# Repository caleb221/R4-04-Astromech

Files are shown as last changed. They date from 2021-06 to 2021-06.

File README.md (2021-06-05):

# R4-04-Astromech
A small Astromech droid I decided to make
  
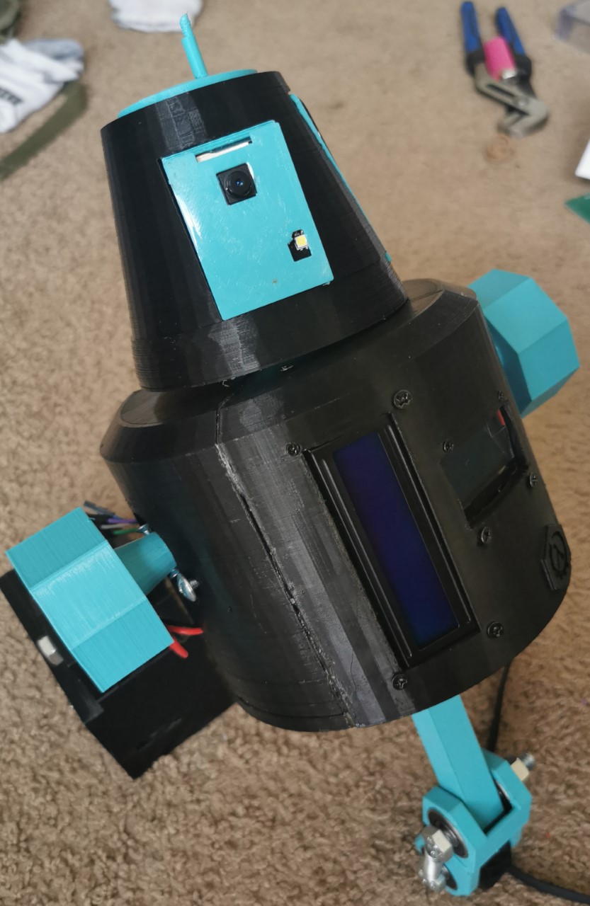
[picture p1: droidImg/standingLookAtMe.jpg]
the droid


# IN PROGRESS! CHECK BACK FOR UPDATES!
   --> finishing up the .ino control code, but hardware and ESP32 code is finished!
   
# Description  
 <h2>This is R4-04!</h2> <br>Designed with the <a href="https://starwars.fandom.com/wiki/R4_astromech_droid">R4 Astromech droid</a> in mind, but getting lost along the way resulted in R4-04, the droid for a galaxy not so far away.<br>
 This droid hosts its own WiFi network, and anyone in reach can accesss a web server holding a livestream of the IP camera and controls for the droid.<br>
 The IP of the droid's control server is printed on the bright blue LCD screen.<br>
 The droid is controlled using websocket communication on the ESP32 and relays information from the user to an Arduino Mega  controlling the motors via I2C commands. The Arduino also handles a self balancing routine, adjusting its shoulders with PID so that rougher terrain won't be a problem.<br> 
Along with the motor control, R4-04 also shows information concerning its environment on a second screen. The information is obtained via a BME280 Sensor.          

# Web App
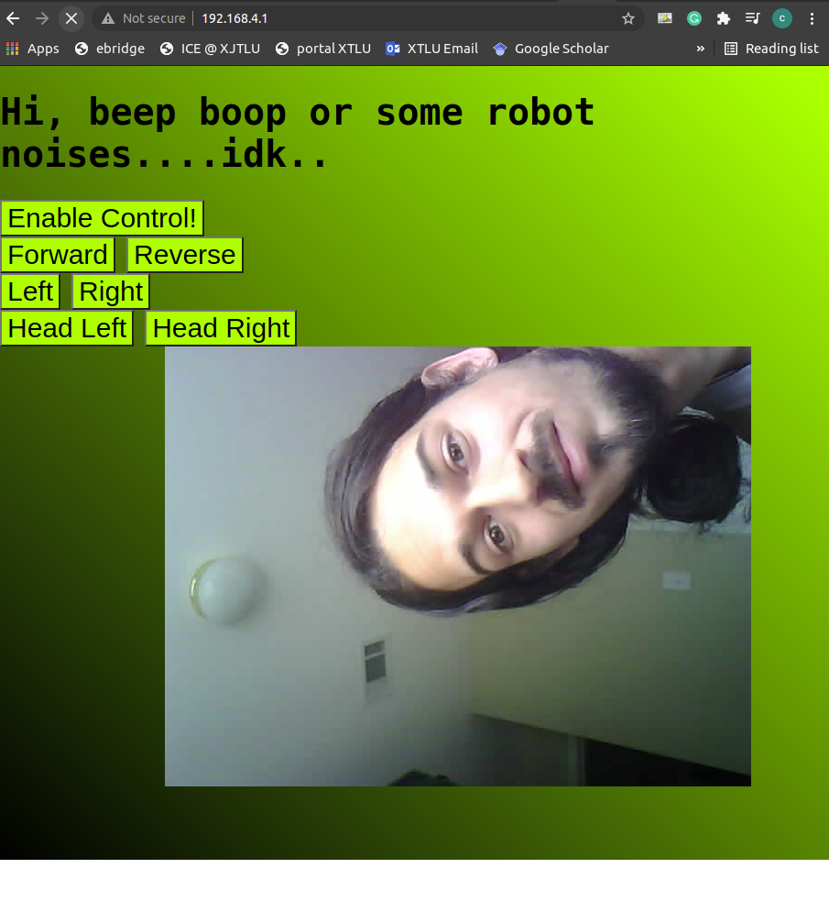
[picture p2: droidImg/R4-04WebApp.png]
the webApp

The droid implements a simple web application to control it along with a live video feed.
The feed is implemented using a timed function to poll the server to update it. It is sent in Jpeg format from the ESP32's onboard  OV2640 camera.<br>
The control buttons are implemented using websocket communication.<br>
Each button is given a specific ID command, which is passed through to the ESP32's I2C wires and sent to the arduino.<br>
Upon a new command event on the I2C wires the Arduino will perform the desired motor operations.

--> a CSS Transform on the img and possible pretty-ing up of the UI should be done in V2

# Stack
ESP32 Components:

    ESP-CAM
    ESP-WiFi
    SPIFFS
    freeRTOS
    I2C Driver
    HTTP-Server
 IDF-Version:
 
    ESP-IDF v4.4-dev-744-g1cb31e509

Arduino:
  
    Unistep2
    AdaFruit BME280
    GY521
    Wire
    U8G2Lib

# Hardware / Materials
    AI-Thinker ESP32-CAM 
    Arduino Pro Mega 2650 
    I2C 1602 LCD (blue) 
    I2C 1.3'' LCD Screen (white) 
    GYU-521 Accelerometer and Gyroscope 
    BME280 
    28byj-48 Stepper motor and 2003 ULN Driver (X3)
    L298N DC Motor Driver 
    DC "TT" Motor and wheel (X2)
    5V 30mA Mini Solar Panel 50x33mm (x2)
    4.8V NiMh 2200 mAh Battery (x2)
    608 Abec 9 Bearings (x8)<br>
    M4 X 30mm Screw and nuts X 6
    M3 x 35mm Screws X 4<br>
    M3 X various smaller sizes X 16
    5/16'' Bolt and nut (2.5+inches) X3 
    Springs that fit over the 5/16'' bolt (these are optional but help)
    Dupont Wires (Mostly Female to Female, but a Few male to Female)
    Various proto boards cut to size
    some passive components listed in the schematic
    Epoxy glue
    Hot glue 
    Solder
    PETG (testing parts took a lot of filament, not sure what the end result requires, also PLA should be fine)<br>

  # Tools
    3D printer (designed with the ender 3 in mind)
    Soldering Iron
    Screwdriver
    Hot Glue Gun
    Files / post processing tools
    Wire cutter
    A ventilated area
    Socket Wrench / Sockets come in handy 
    Something to spread epoxy with 
    Hacksaw
  
  # Schematic
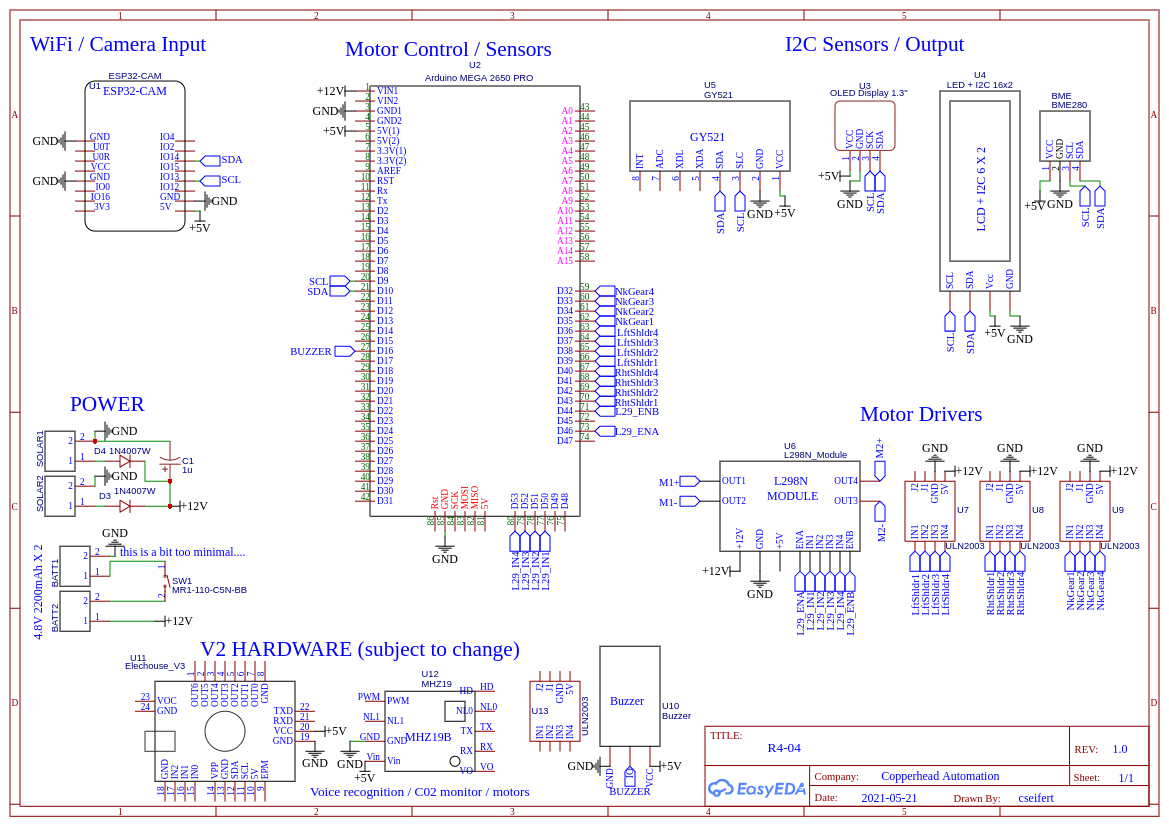
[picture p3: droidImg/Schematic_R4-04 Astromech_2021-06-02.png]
A simple schematic


# 3D Printer Settings

    Printer: Creality Ender 3 pro V2
    Filament: Duramic PETG
    Infill: 20% 
    Support: 2% everywhere
    Temp: 235
    Slicer: Cura
--> Slow on the first layer<br>
--> PLA Should be just fine for the parts as well, i just had PETG because it was cheaper at the time.<br>

# STL / FREECAD FILES
I designed the droid using FreeCAD, which is free and works on all major OS platforms.<br>
You are free to edit / change all designs, but please give a reference to the original!<br>
Printing all parts goes like this:<br>

    2 droidSolarPanelHolder1.stl, 1 of all others in the UPPER folder (head / neck)
    2 legs, 2 Shoulders, 2 FourthLeg_body.stl (Stepper holders), and 1 of each on the rest in the MIDDLE folder. (main body)
    2 droidFoot1.stl, 1 of each 3rd foot component in the LOWER folder. (lower assembly)

# Wiring / Testing

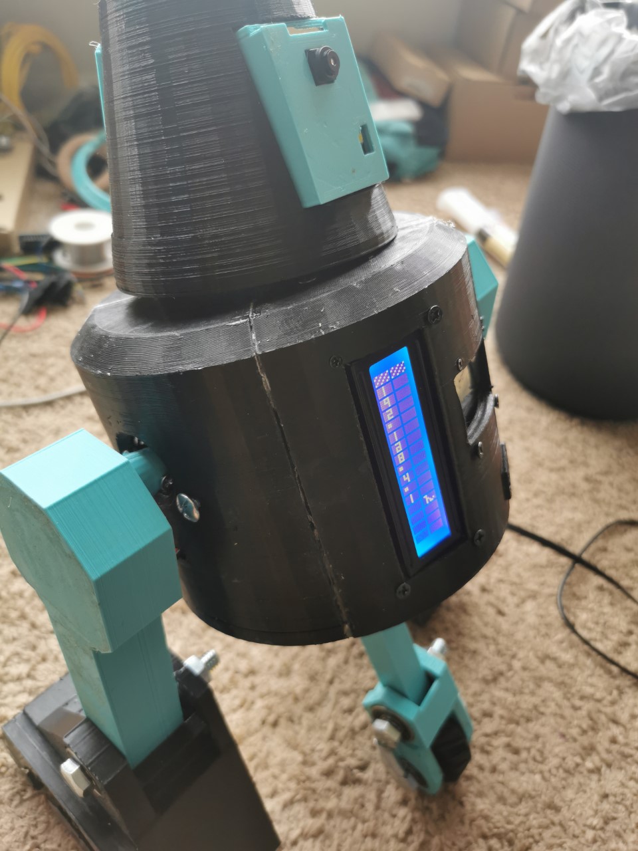
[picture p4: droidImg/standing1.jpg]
the droid
 

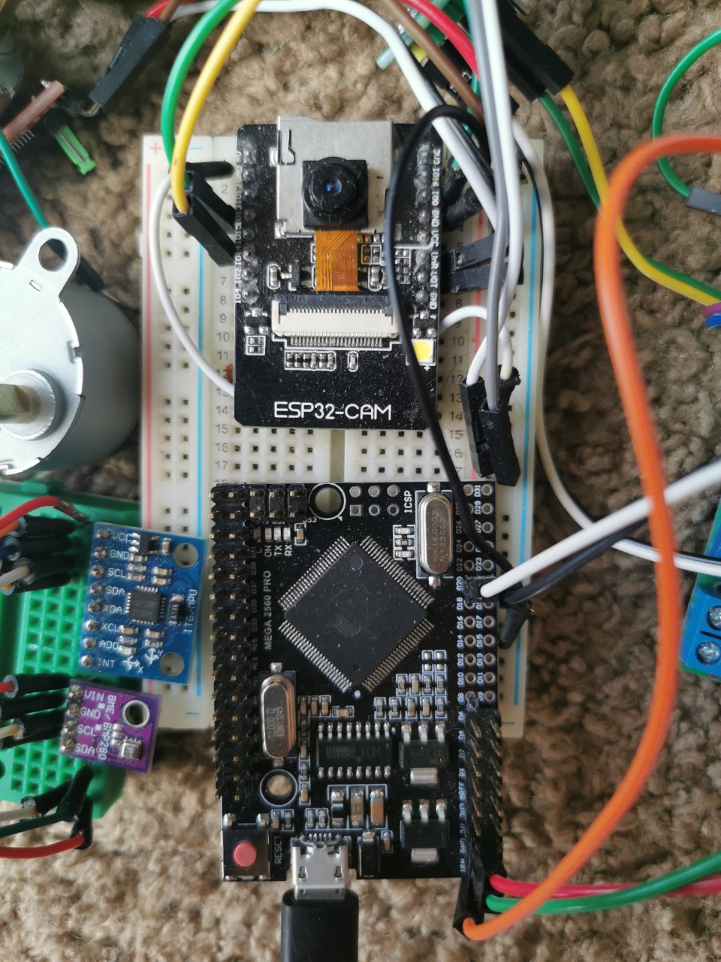
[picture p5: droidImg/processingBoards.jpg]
droid brain and heart
   
   
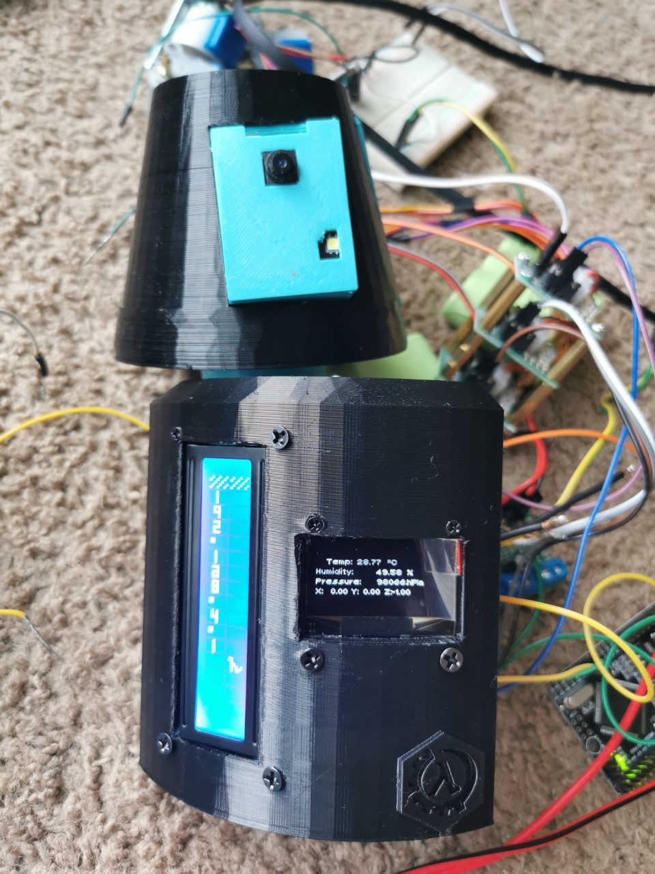
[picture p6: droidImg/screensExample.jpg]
Screen Test


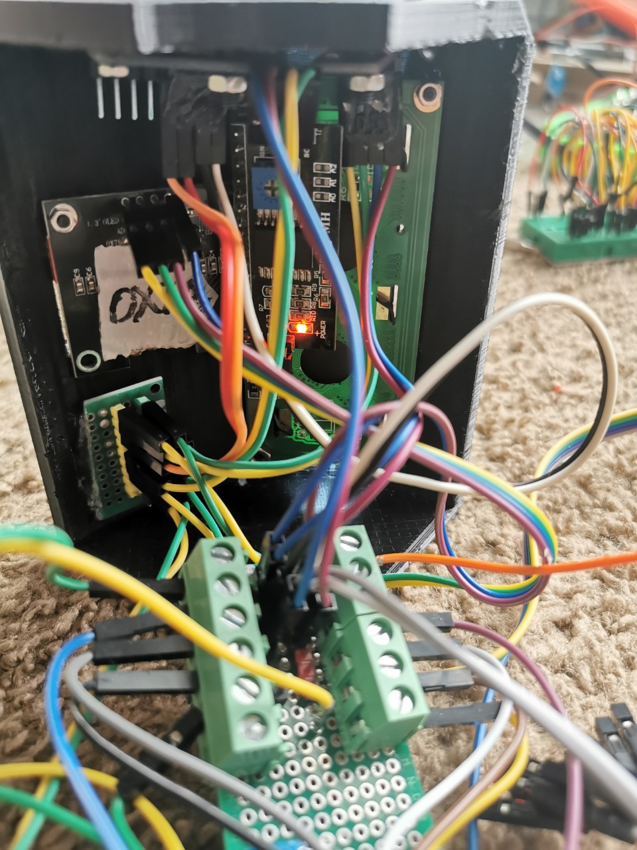
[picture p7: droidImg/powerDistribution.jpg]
   

# Mechanical Notes
The TT motor and wheel attatch to the foot using  M3 X 35MM screw and nuts. The leg is attached using 2 bearings and a 5/16'' bolt and nut.
There is a hole for the wires in the middle of the foot, as well as a space for them to fit on the side of the leg.<br>
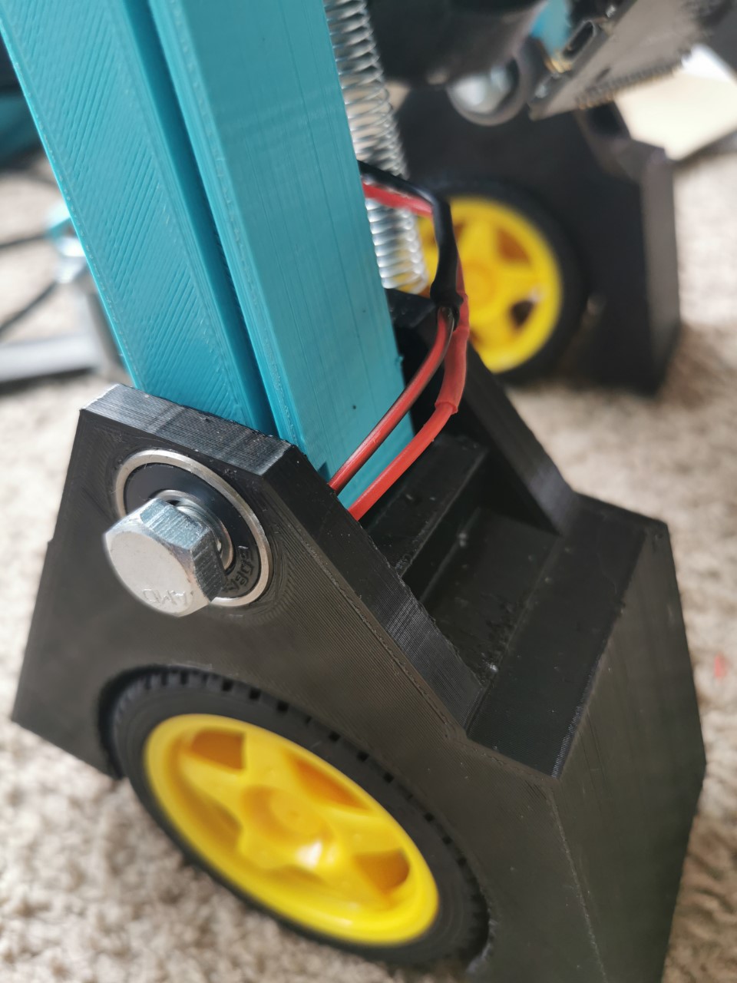
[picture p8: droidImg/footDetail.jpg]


<br>
The backside view of the droid.
There is a door that utilizes an M3 X 20 screw to hold both pieces in place.
Springs are attached from the stepper motor's M4 screw to the Foot's 5/16'' bolt. These are optional but help the droid remain standing under its own weight. The M4 screws I used hindered the neck from reaching the gear, this will be fixed in V2.
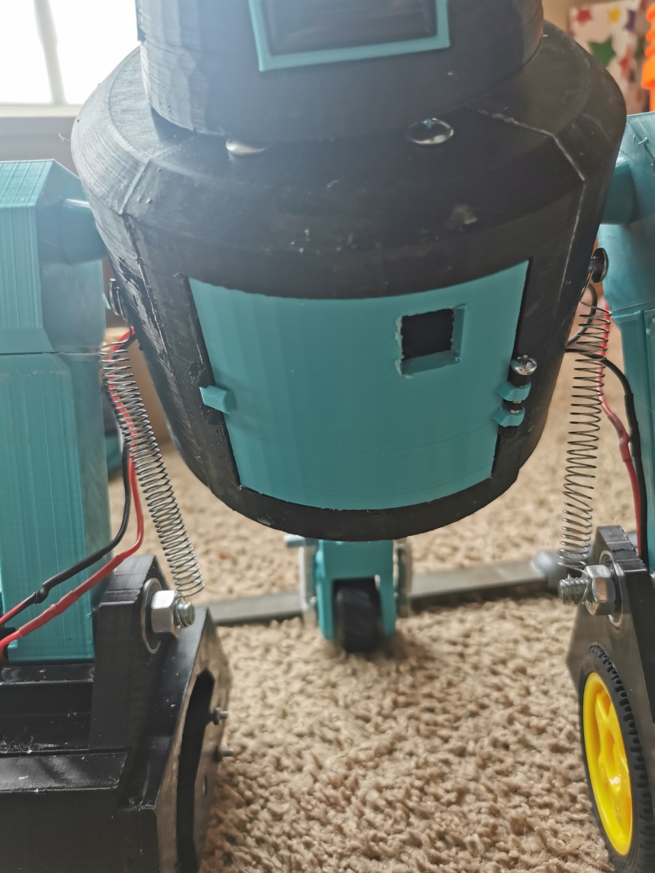
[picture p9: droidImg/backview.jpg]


<br>
There is a stepper motor with the smaller neck control gear attached to the top of the body using M4 screw and nuts. <br>
The neck assembly is glued into place on the head and is not glued to the body. SDA,SCL, 5V, and GND are run through the neck to reach the ESP32-CAM.<br>
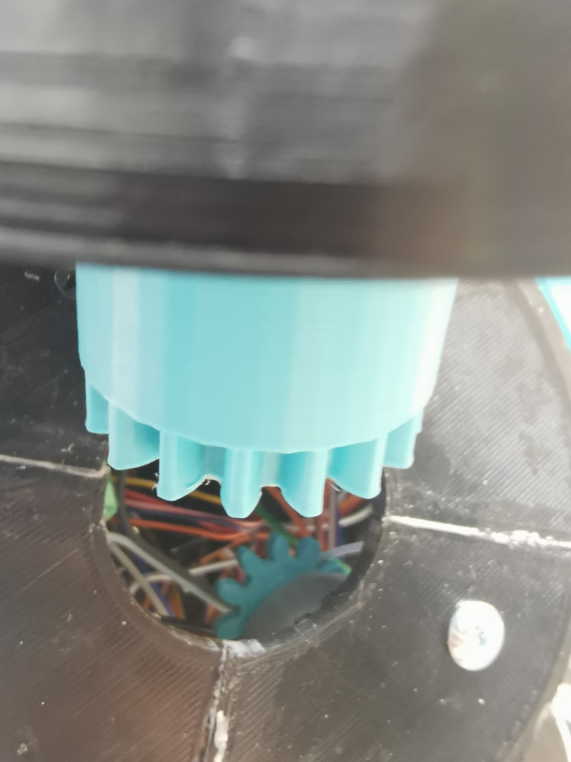
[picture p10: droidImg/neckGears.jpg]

<br>
The Front foot uses 4 bearings and an M3 x 8mm nut and screw that fits in the middle. Along with 2 5/16'' bolts to hold the wheel and leg in place. The springs are attached on the outside of each bolt which help restrict the freedom of movement.
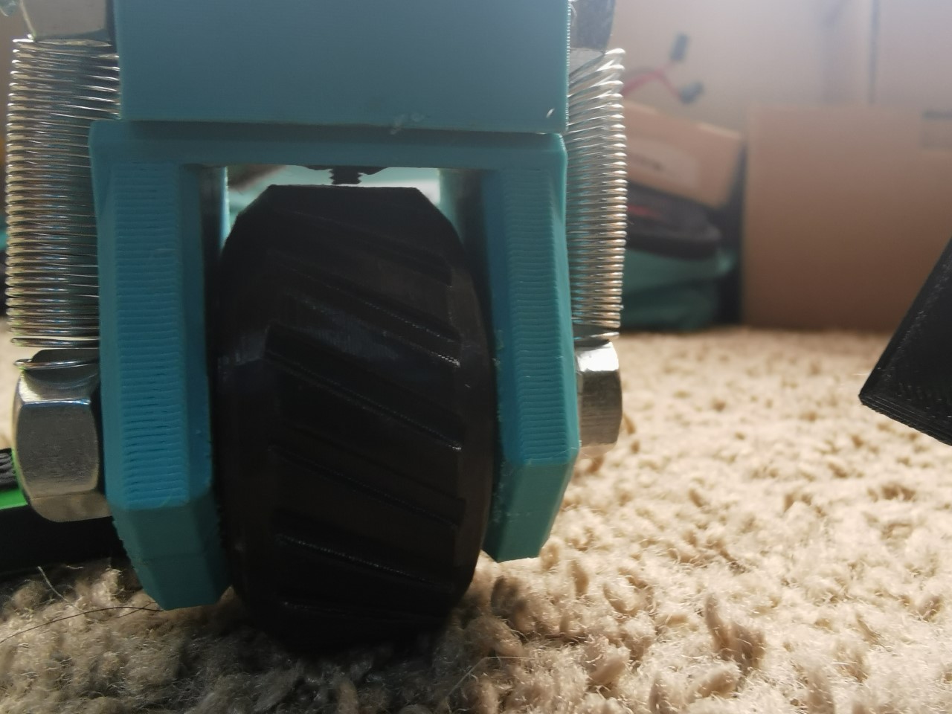
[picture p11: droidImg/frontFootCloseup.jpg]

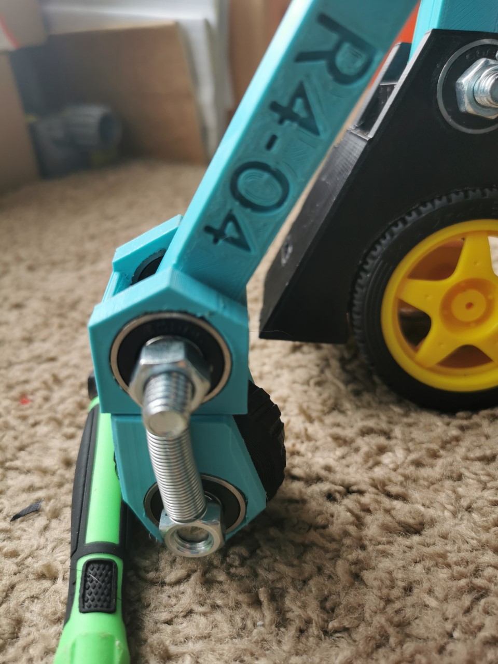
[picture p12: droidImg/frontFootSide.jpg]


# V2 Notes for the future
  As with everything, theres always something to upgrade or clean up.<br>
  Here's a list of things I've thought of to work on if a second version is going to be built. 

 Hardware upgrades:
  
    Voice Recognition Module (elecHouse)
    Buzzer
    Stepper motor for 3rd Leg
    Distance Sensors
    More Environmental Sensors
    **POSSIBLY** Replace ESP32 with orange/Raspberry Pi
    Arc Generator (would also require Linear Actuator)
    Change DuPont wires to something that connects better (MOLEX/JST/something)
    ***Fix up power components** (5V is being fed through the Arduino's Regulator, causing current bottleneck)
    
Software Upgrades:

    Web app CSS needs to transform the Image vertically and make things prettier
    Send Environmental Data to web UI
    logging??
    Give additional hardware options on web UI
    train elecHouse voice module to recognize commands

 Mechanical Upgrades:
 
    Combine 3/4ths of the body into 1 .stl
    Body can be taller
    create spaces in body for hardware components (slots, screw holes, etc.)
    Figure out a 3Rd leg drive mechanism (leg also needs to fit in the body)
    change direct stepper connection to shoulders into something better (timing belts??)

# Disclaimer:
 This R4 Unit is a personal voyage in learning freeCAD and helped me form a new curriculum for a Robotics Class.<br>Also, I wanted another ESP32-CAM project, they're too much fun!<br>
 It is not in any way meant to represent work of Disney, Star Wars, or any legal stuff. I don't know how to put this correctly, but its not a 501st worthy model. But still fun to build!

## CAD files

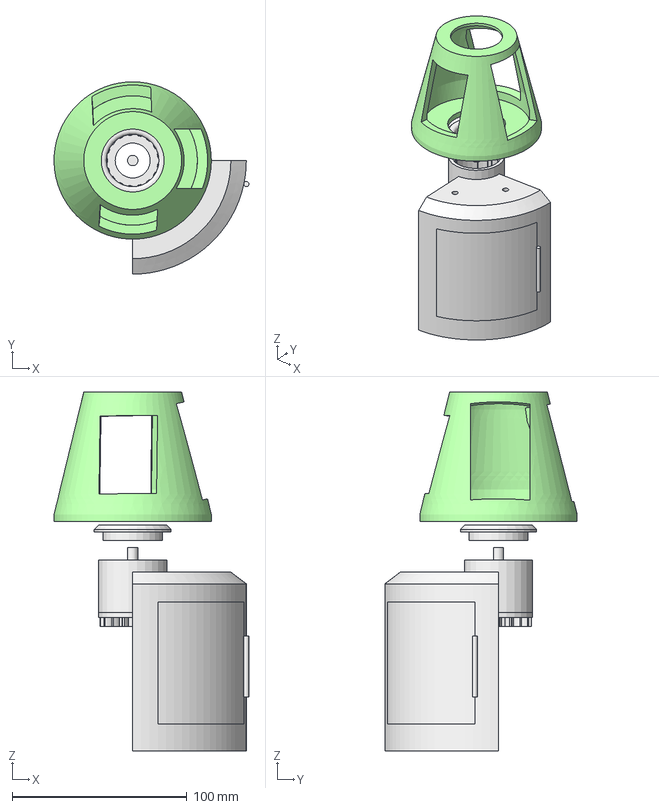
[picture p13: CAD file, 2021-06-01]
FREECAD/droidNeckGear_v1.FCStd
111.5 x 110.0 x 205.3 mm
Spur Gear (24 teeth)
Spur Gear (8 teeth)
Spur Gear (22 teeth)
Spur Gear (11 teeth)
Spur Gear (9 teeth) (1)
droidHead1TEST

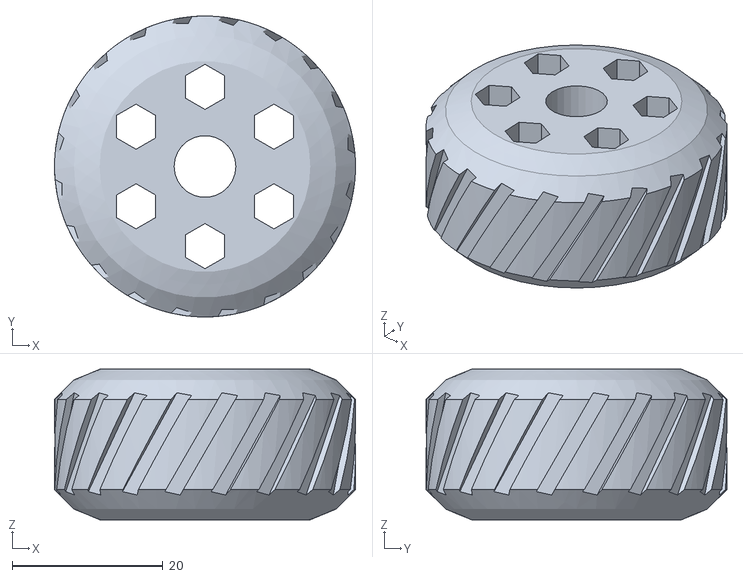
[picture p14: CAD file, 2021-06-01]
STL/LOWER/droid3rdWhl_whl.stl
40.0 x 40.0 x 20.0

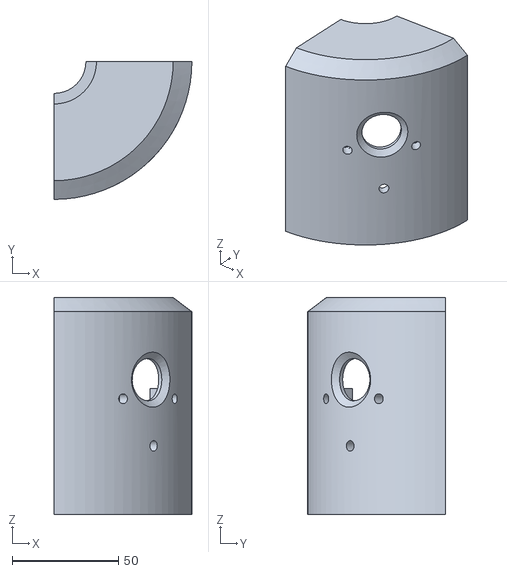
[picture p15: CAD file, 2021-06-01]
STL/MIDDLE/fourthLEG_body.stl
65.0 x 65.0 x 102.3

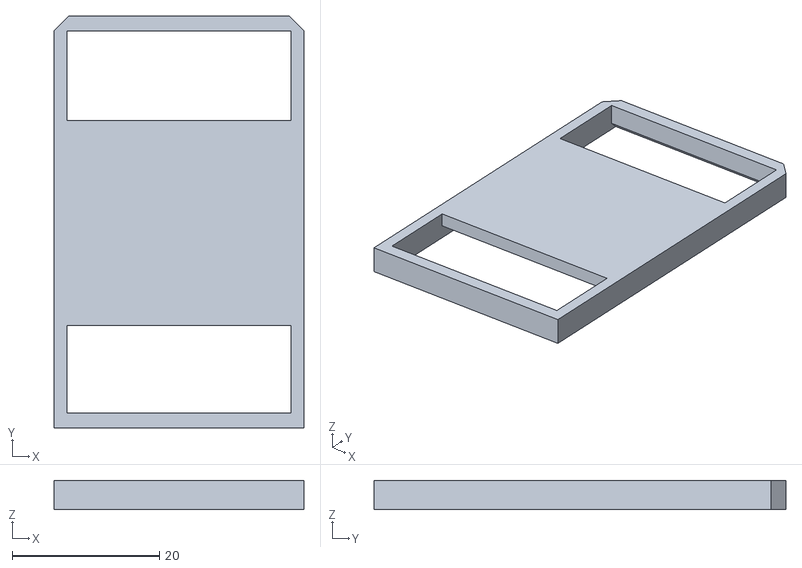
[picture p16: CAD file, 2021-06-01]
STL/UPPER/droidSolarPanelHolder1.stl
34.0 x 56.0 x 4.00

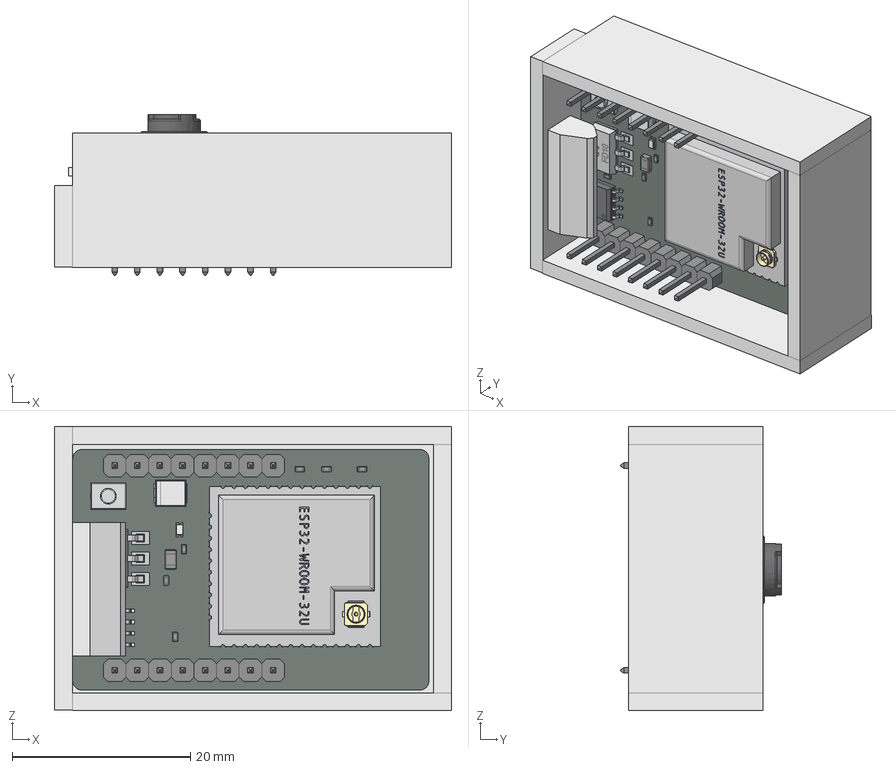
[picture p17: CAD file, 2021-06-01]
FREECAD/esp32CAM_holder1.FCStd
44.6 x 18.1 x 31.9 mm
Pin Header 4 x 1 TH 2.54mm Pitch v1
Pin Header 4 x 1 TH 2.54mm Pitch v002
Pin Header 4 x 1 TH 2.54mm Pitch v003
Pin Header 4 x 1 TH 2.54mm Pitch v004
u
capacitor-CAPM-TANTB-YL v1
switch-3x4x2mm - 2 Pad v1
nano - reg
icbody
Component5(Mirror)
Component5(Mirror)001
Component5(Mirror)002
Component5(Mirror)003
resistor-NTC-0402-T0.6 v1
resistor-NTC-0402-T0.6 v002
resistor-NTC-0402-T0.6 v003
resistor-NTC-0805-T1.3 v1
resistor-NTC-0402-T0.6 v004
resistor-NTC-0402-T0.6 v005
resistor-NTC-0402-T0.6 v006
resistor-NTC-0402-T0.6 v007
smd-transistor-SOT23-3 v1
smd-transistor-SOT23-3 v002
resistor-NTC-0402-T0.6 v008
resistor-NTC-0402-T0.6 v009
resistor-NTC-0402-T0.6 v010
LED SMD 5050 White v1
resistor-NTC-0402-T0.6 v011
resistor-NTC-0402-T0.6 v012
resistor-NTC-0402-T0.6 v013
resistor-NTC-0402-T0.6 v014
resistor-NTC-0402-T0.6 v015
resistor-NTC-0402-T0.6 v016
resistor-NTC-0402-T0.6 v017
capacitor-CAPC-0603-T0.9-BN v1
resistor-NTC-0402-T0.6 v018
capacitor-CAPC-0603-T0.9-BN v002
smd-transistor-SOT23-3 v003
connector smd usl00-20l_p0-4_l12-6_w2-75 v1
resistor-NTC-0402-T0.6 v019
resistor-NTC-0402-T0.6 v020
smd-transistor-SOT23-3 v004
sdreader
Micro SD-Card v1
User Library-ov9655_ov9655_flex_pcb
User Library-ov9655_ov9655_flex_reinf
User Library-ov9655_ov9655_back_panel
User Library-ov9655_ov9655_body
User Library-ov9655_ov9655_lens

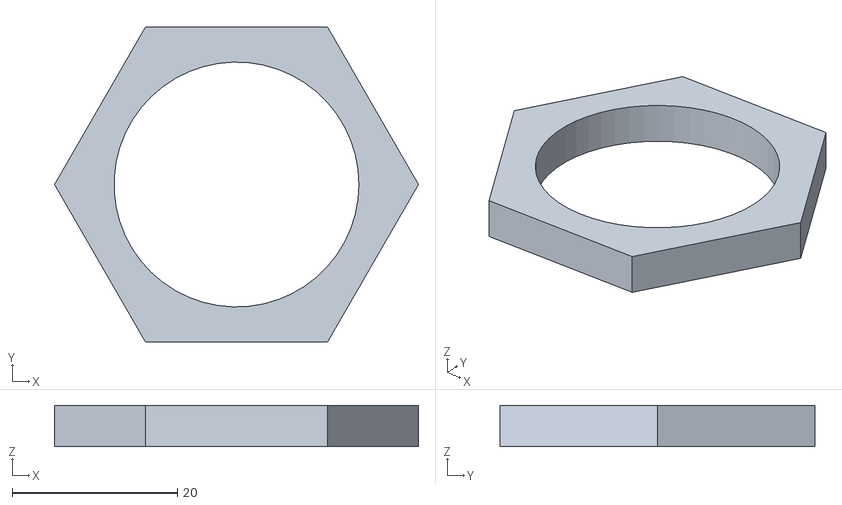
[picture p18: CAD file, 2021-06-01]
STL/LOWER/droidBtmPlug2.stl
44.0 x 38.1 x 5.00

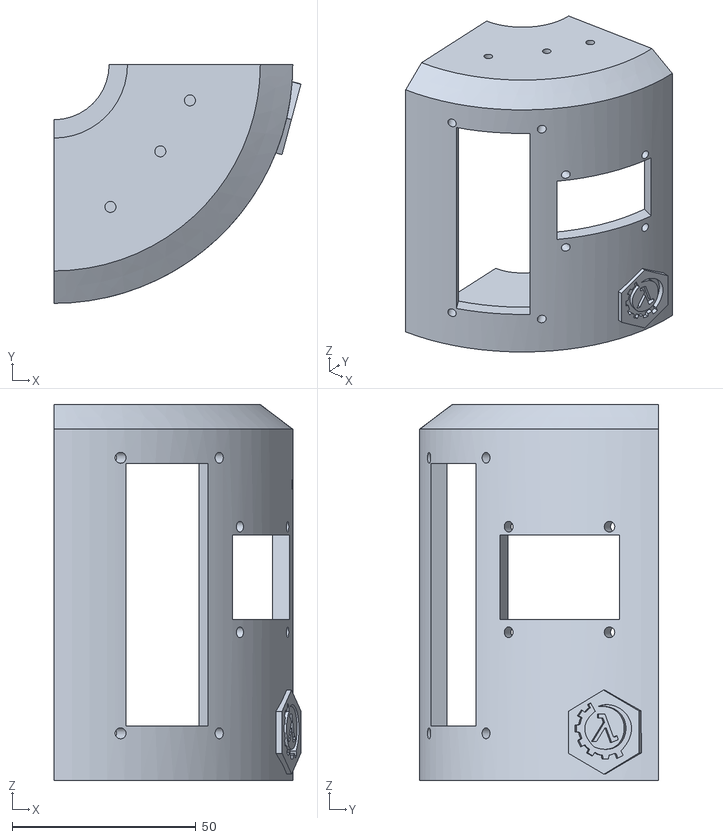
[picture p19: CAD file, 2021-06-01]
STL/MIDDLE/fourthFRONT_body.stl
67.2 x 65.0 x 102.3

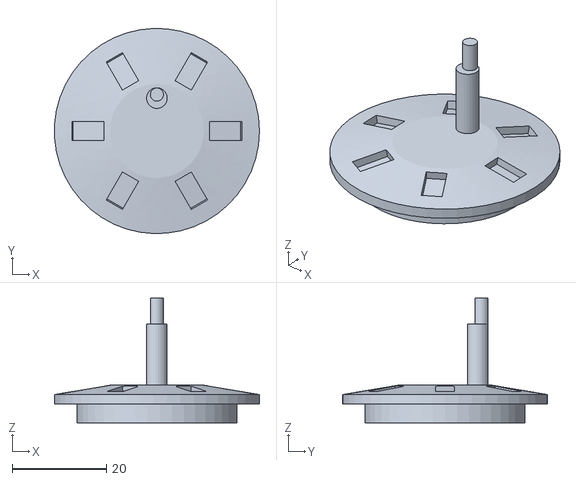
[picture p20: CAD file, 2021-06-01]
STL/UPPER/droidHeadCAP_v1.stl
43.6 x 43.6 x 26.5

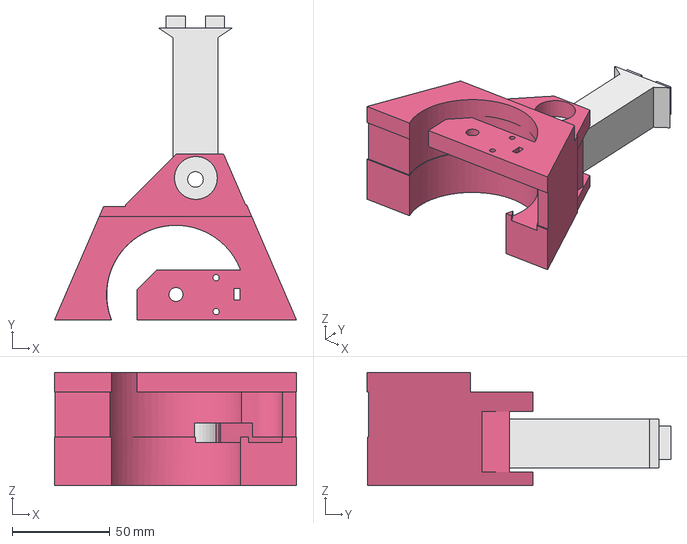
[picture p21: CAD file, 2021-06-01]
FREECAD/droidLEGv1.FCStd
124.1 x 155.7 x 58.0 mm
droidFOOT_test1

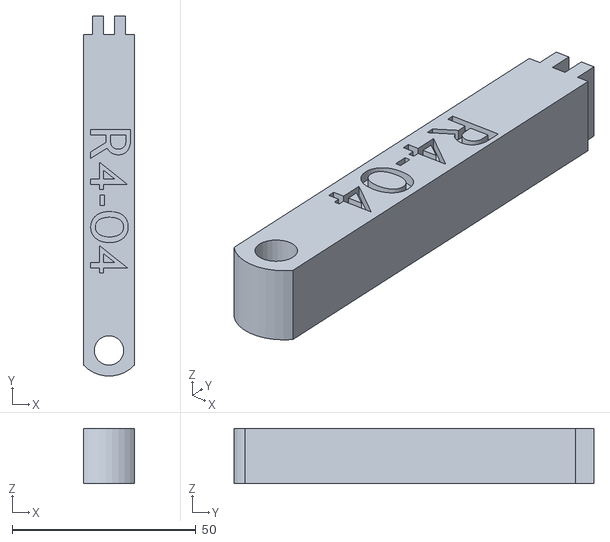
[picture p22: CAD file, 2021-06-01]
STL/LOWER/droid3rdLeg.stl
14.0 x 98.0 x 15.0

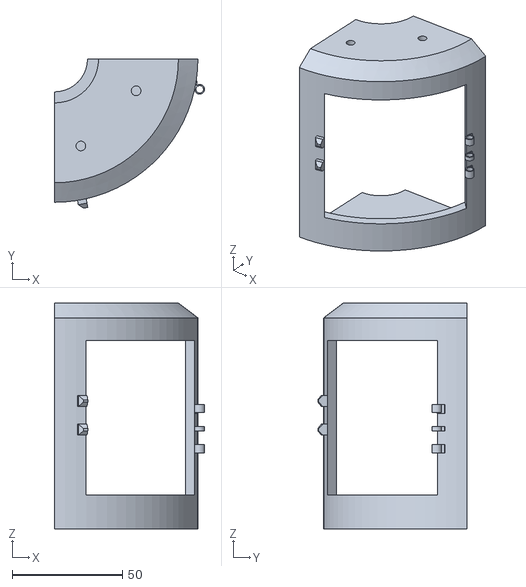
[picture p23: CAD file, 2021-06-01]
STL/MIDDLE/fourthBACK_body.stl
68.0 x 67.7 x 102.3

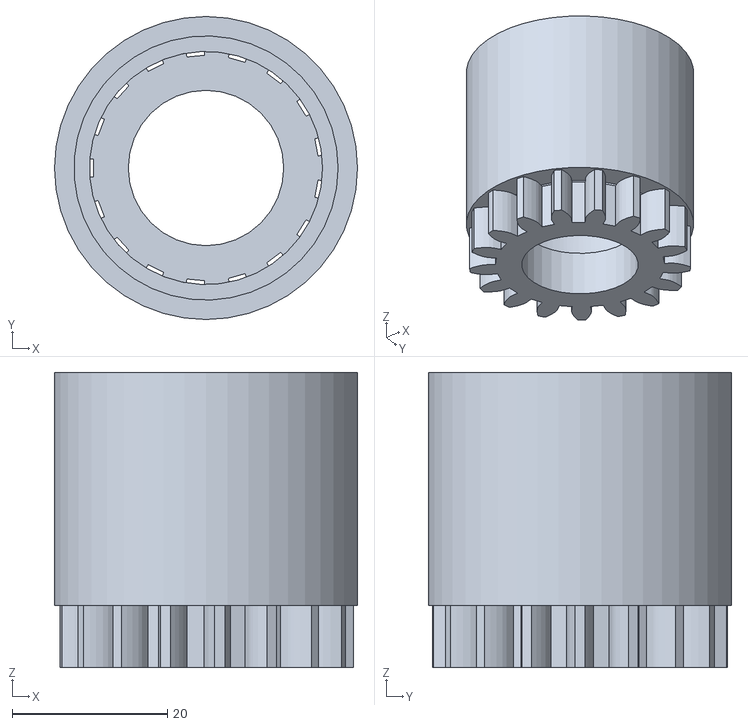
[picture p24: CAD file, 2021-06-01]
STL/UPPER/droidNeckGear_BG.stl
39.0 x 39.0 x 38.0

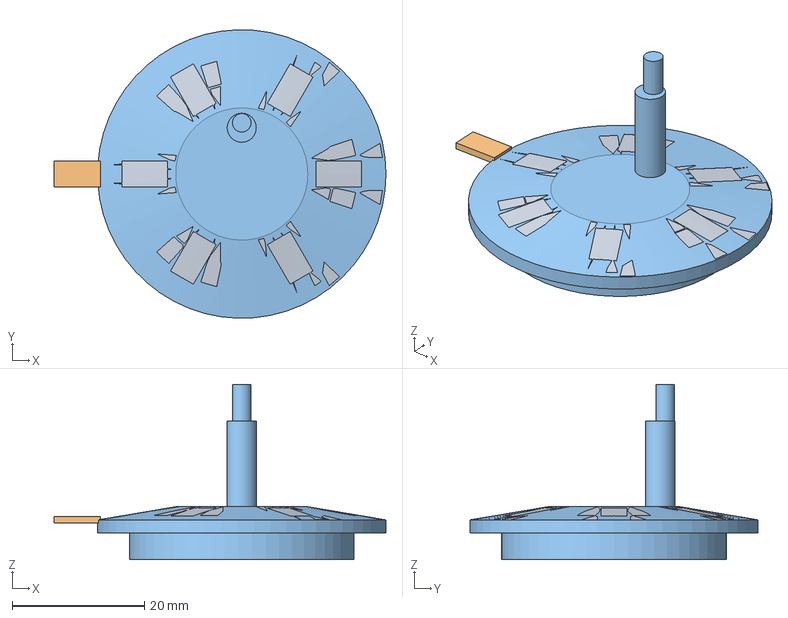
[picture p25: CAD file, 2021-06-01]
FREECAD/droidHeadCap1.FCStd
50.2 x 43.6 x 26.5 mm

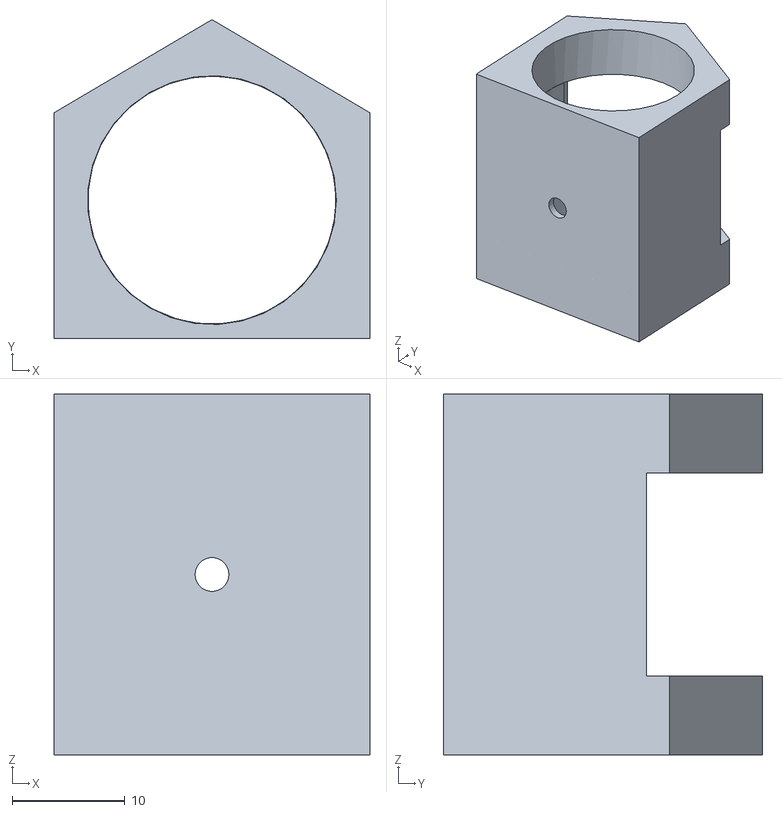
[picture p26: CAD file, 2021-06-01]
STL/LOWER/droid3rdWhl2.stl
28.0 x 28.3 x 32.0

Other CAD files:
STL/MIDDLE/droidBackDoor.stl
STL/UPPER/droidHead1.stl
FREECAD/solarPanelHolder1.FCStd
STL/LOWER/droidFoot1.stl
FREECAD/droid3RdLegBottomWheel.FCStd
FREECAD/droid3rdLegV2.FCStd
FREECAD/droidBtmRing.FCStd
FREECAD/droidShoulderV2.FCStd
FREECAD/droidV2FOOT.FCStd
FREECAD/headCone1.FCStd
STL/LOWER/droid3rdWhl_holder.stl
STL/LOWER/droidBtmPlug1.stl
STL/MIDDLE/droidBtmRing2.stl
STL/MIDDLE/droidLEG_v1.stl
STL/MIDDLE/droidShlder2.stl
STL/UPPER/droidEsp32Holder2.stl
STL/UPPER/droidNeckGear_CP.stl
STL/UPPER/droidNeckGear_SM.stl

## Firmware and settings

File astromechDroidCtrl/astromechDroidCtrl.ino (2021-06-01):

//==============================================
//            ASTROMECH DROID HEART
//==============================================
//
// Arduino Mega2560-pro 
//
// movement 
//  -2 DC motors
//  -3 Servo Motors
//   
// sensors
// Voice Recognition Module (maybe)
// BMP280
// C02 Sensor
//  
//
// Buzzer
// i2c Screen 1.3''
// i2c interrupt slaved
//  ESP32-CAM is MASTER (webCtrl)


//sensor libraries
#include<BH1750.h>
#include "MHZ19.h"
#include "GY521.h"
#include <Adafruit_Sensor.h>
#include <Adafruit_BME280.h>
#include<Wire.h>
#include <Unistep2.h>

#include <U8g2lib.h>


//L298N DC Motor Pins

#define en1 44 //D49 
#define en2 46//D48

#define in1 50//D50
#define in2 51//D51
#define in3 49//D52
#define in4 48//D53


#define HEART_ADDRESS 0x5F//I2C Adress for HEART

#define BUZZER_PIN 6
//screen settings
//.96'' I2C
//U8G2_SSD1306_128X64_NONAME_F_HW_I2C u8g2(U8G2_R0, /* reset=*/ U8X8_PIN_NONE);
//1.3'' I2C
U8G2_SH1106_128X64_NONAME_F_HW_I2C u8g2(U8G2_R0, /* reset=*/ U8X8_PIN_NONE);

#define SEALEVELPRESSURE_HPA (1013.25)



const int stepsPerRevolution = 2048;  // change this to fit the number of steps per revolution
//Stepper shoulderRight(stepsPerRevolution, 43, 42, 41, 40);
//Stepper shoulderLeft(stepsPerRevolution, 39, 38, 37, 36);
//Stepper neckStepper(stepsPerRevolution, 35, 34, 33, 32);

Unistep2 shoulderRight(43, 42, 41, 40, 2048, 1000); // pins for IN1, IN2, IN3, IN4, steps per rev, step delay(in micros)
Unistep2 shoulderLeft(39, 38, 37, 36, 2048, 1000);
Unistep2 neckStepper(35, 34, 33, 32,2048,1000);


GY521 gyro(0x68);
Adafruit_BME280 bme280;
//Control Globals (switched on I2C event)
bool hasCmd = false;
static int  usrCmd = 0;

// 0 - NOTHING
// 1 - FORWARD
// 2 - REVERSE
// 3 - RIGHT
// 4 - LEFT
// 5 - HEAD_LEFT
// 6 - HEAD_RIGHT

// Data globals
float humid;
float temp;
float c02;
float pressure;
float imuX;
int gyrox,gyroy,gyroz;

//Voice timers
const long toneInterval;
boolean outputTone = false;
unsigned long previousToneTime;
  int toneOut[8];
  int toneTimes[8];
  int thisNote=0;

// STATE MACHINE CONTROLS
unsigned long currentTime;
unsigned long previousTime;
double elapsedTime;
double lastErr;
double error, totError,rateError;


//PID CONSTANTS
double kp=2;
double ki=5;
double kd=1;
float setPoint;



void setup() {
Serial.begin(9600);
  //i2c setup
  Serial.println("hi!");

/*=======
 * MOTOR TEST
 */

  
  Wire.begin(HEART_ADDRESS);
  Wire.onReceive(getFromHead); // register event
    
  if(!  u8g2.begin()){
//display.begin(SSD1306_SWITCHCAPVCC, 0x3C)) { 
    Serial.println(F("SSD1306 allocation failed"));
   // for(;;); // Don't proceed, loop forever
  }

//GY521 GYROSCOPE/ACCELEROMETER (only used for gyro)
if(gyro.wakeup()==false)
{
    Serial.print(millis());
    Serial.println("\tCould not connect to GY521");
    delay(1000);
 }
 
//BME 280 TEMP/HUMIDITY
if(!bme280.begin(0x76))
    {
     Serial.print("BME NOT FOUND");
     //while(1);   
    }   
  //

  
  setPoint = 0;
//*/


  //L298N setup
  pinMode(in1, OUTPUT);
  pinMode(in2, OUTPUT);
  pinMode(in3, OUTPUT);
  pinMode(in4, OUTPUT);

  //buzzer pin
  //pinMode(BUZZER_PIN,OUTPUT);

//init and calibrate


  //noTone(BUZZER_PIN);
  digitalWrite(in1, LOW);
  digitalWrite(in2, LOW);
  digitalWrite(in3, LOW);
  digitalWrite(in4, LOW);

//gyroscope
  gyro.setAccelSensitivity(0);  // 2g
  gyro.setGyroSensitivity(0);   // 250 degrees/s
  gyro.setThrottle();

  // set callibration values from calibration sketch.
  gyro.gxe = 6.208;
  gyro.gye = -0.863;
  gyro.gze = -0.004;

Serial.println("All setup!");

}

void loop() {
  // put your main code here, to run repeatedly:

currentTime = millis();



//Serial.println(thisNote);

//voiceControl(0);

if(hasCmd)
{
  /*
  switch(cmd)
  {
  case 0:
    
  break;  
  default:
  break;  
  }
*/
  

  //int balancer = computePID(gyrox);
  //moveStepper(balancer)

  
}


  
  //readBME();
  //readGyro();
  //screenControl(0);


  float myPID = computePID(gyrox);
  Serial.println(myPID);
//stepperTurn(1,0.1);
//  delay(200);
  
 // Serial.println("SHOULDER FORWARD");
  //stepperTurn(0,30);



  //Serial.println("SHOULDER BACKWARD");

 // stepperTurn(1,10);
  
 //float myPID = computePID(gyrox);
 //Serial.print("\nPID:: ");
 //Serial.print(myPID);
  //delay(200);
  
  
 
  stepperTurn(2,20);



  //stepperTurn(0,2);
//Serial.print("\n\nGYRO X:");
//Serial.print(gyrox);
//Serial.print("\n");
/*
if(thisNote > 8)
{
  voiceControl(0);
}
else
{
  voiceControl(1);
} 
*/

/*
Serial.print("\n\nGYRO X:");
Serial.print(gyrox);
Serial.print("\nGYRO Y:");
Serial.print(gyroy);
Serial.print("\nGYRO Z:");
Serial.print(gyroz);
Serial.print("\nTEMPERATURE: ");
Serial.print(temp);
 Serial.print("\nHUMIDITY:");
Serial.print(humid);
Serial.print("\npressure:");
Serial.print(pressure);
delay(1000);
*/

//wheelTurn(100,0);
//Serial.println("turning? 0");
//delay(1000);

//wheelTurn(0,0);
//delay(1000);
//Serial.println("TURNING 1");
//wheelTurn(150,0);
//delay(1000);




//wheelTurn(200,1);
//delay(1000);



/*
  digitalWrite(in1, HIGH);
  digitalWrite(in2, LOW);
  
  digitalWrite(in3, HIGH);
  digitalWrite(in4, LOW);
  analogWrite(en1,150);
  analogWrite(en2,150);

  
  delay(1000);

  digitalWrite(in1, LOW);
  digitalWrite(in2, HIGH);


  digitalWrite(in3, LOW);
  digitalWrite(in4,HIGH);
 analogWrite(en1,200);
  analogWrite(en2,200);
delay(1000);
*/


//delay(1000);

//Serial.println("looped");
}

//========================================================================
//                         COMMAND PROCESSING
//========================================================================


// function that executes whenever data is received from master
// this function is registered as an event, see setup()
void getFromHead(int len)
{

  char message [len];
  int i=0;
  while(0 < Wire.available()) // loop through all but the last
  {
    char c = Wire.read(); // receive byte as a character
    Serial.print(c);         // print the character
    message[i]=c;
    i++;
  }

if(message[0] =='f') //FORWARD
{
  hasCmd = true;
  usrCmd = 1; 
}
else if (message[0] =='l') //LEFT 
{
    hasCmd = true;
    usrCmd = 4;
  
}

else if (message[0] =='r' && len ==0) //RIGHT
{
    hasCmd = true;
    usrCmd = 3;
}
else if (message[0] =='r' && message[1]=='r') //REVERSE
{
    hasCmd = true;
    usrCmd = 2;
}
else if (message[0] =='h' && message[1]=='l') //HEAD LEFT
{
    hasCmd = true;
    usrCmd = 5;
}
else if (message[0] =='h' && message[1]=='r') //HEAD RIGHT
{
    hasCmd = true;
    usrCmd = 6;
}
else //DUNNO, SOMETHING MESSED UP?
{
    message[0]='\0';
    hasCmd = false;
    usrCmd = 0;
  
}
/*  switch statement for 
 *  commands from esp32
 *  figure out a good sending scheme
 *  switch on scheme
 *      case write to functions with proper params
 *       or return data if need be
 */

//send data with:
//Wire.write("data");
  
  //char x = Wire.read();    // receive byte as an integer
  // Serial.println(x);         // print the integer


}

//========================================================================
//                         SENSOR READINGS
//========================================================================
void readGyro()
{
   if( gyro.read() == GY521_OK)
   {
   gyrox = gyro.getGyroX();
   gyroy = gyro.getGyroY();
   gyroz = gyro.getGyroZ(); 
   }
   else
   {
    //TELL THE GYRO TO WAKEUP!
    Serial.println("GYRO FAILED TO READ");
    gyro.wakeup();
    gyro.setAccelSensitivity(0);  // 2g
    gyro.setGyroSensitivity(0);   // 250 degrees/s
    gyro.setThrottle();
    gyro.gxe = 6.208;
    gyro.gye = -0.863;
    gyro.gze = -0.004;
    return;
   }
   
}

void readBME()
{
  temp=bme280.readTemperature();
  humid= bme280.readHumidity();
  pressure=bme280.readPressure();
}



//========================================================================
//                         PID CONTROL
//========================================================================

float computePID(float angleIn)
{
  elapsedTime = (double)(currentTime-previousTime);


  if(elapsedTime < 2000)
  {
    Serial.println("RESETTING PID ERRORS!");
    elapsedTime=0;
    error=0;
    lastErr=0;
    
  } 
  error = setPoint -angleIn;
  totError += error*elapsedTime;
  rateError = (error-lastErr)/elapsedTime;
  float out = kp*error+ki*totError+kd*rateError;
  
 return out; 
 }



//========================================================================
//                         OUTPUT CONTROL
//========================================================================



void screenControl(int screenDisp)
{
    u8g2.clearBuffer();
    u8g2.setFont(u8g2_font_tinytim_tf);    
    char buff[15];
      
  u8g2.setCursor(0, 0);
  dtostrf(temp,5,2,buff); 
  u8g2.drawStr(10,20,"Temp: ");
  u8g2.drawStr(40,20,buff);
  u8g2.drawStr(65,20," *C");
  dtostrf(humid,5,2,buff);
  u8g2.drawStr(0,30,"Humidity:");
  u8g2.drawStr(60,30,buff);
  u8g2.drawStr(90,30,"%");
  dtostrf(pressure,5,2,buff);
  u8g2.drawStr(0,40,"Pressure:");
  u8g2.drawStr(60,40,buff);
  u8g2.drawStr(90,40,"hPa");  
 u8g2.drawStr(0,50,"X:");
 dtostrf(gyrox,5,2,buff);
 u8g2.drawStr(10,50,buff);
 u8g2.drawStr(35,50,"Y:");
 dtostrf(gyroy,5,2,buff);
 u8g2.drawStr(42,50,buff);
 u8g2.drawStr(68,50,"Z:");
 dtostrf(gyroz,5,2,buff);
 u8g2.drawStr(75,50,buff);

 
u8g2.sendBuffer();  
   
}

void voiceControl(int voiceOUT)
{
//each 'word' must be be a global number n long
// probably 20, fill the void with 0 s
if(thisNote == 0)
{
  int pSize=0;
  switch(voiceOUT)
  {
   case 0:

int p1[]={ 440, 196, 196, 220, 196, 0, 247, 262};
int pt1[] ={8,8,8,8,8,8,8,8};
    pSize = sizeof(p1)/sizeof(p1[0]);
 for (int i=0;i<pSize;i++)
   {
   toneOut[i]  =p1[i];
    toneTimes[i]=pt1[i];
   } 
  
   break;
   case 1:


int p2[]={ 440, 10, 440, 10, 220, 10,220, 10};
int pt2[] ={8,8,8,8,8,8,8,8};
    pSize = sizeof(p2)/sizeof(p2[0]);
 for (int i=0;i<pSize;i++)
   {
   toneOut[i]  =p2[i];
    toneTimes[i]=pt2[i];
   } 
   
   break;

   default:
int pd[]={ 0, 10, 440, 10, 220, 10,220, 10};
int ptd[] ={8,8,8,8,8,8,8,8};
    pSize = sizeof(pd)/sizeof(pd[0]);
 for (int i=0;i<pSize;i++)
   {
   toneOut[i]  =pd[i];
    toneTimes[i]=ptd[i];
   } 

  
// phraseSelect={0,0,0,0,0,0,0,0};
// phraseTime[]=  {0,0,0,0,0,0,0,0,0,0,0}; 
   break;
  }
}
int noteDuration = 1000 / toneTimes[thisNote];
int pauseBetweenNotes = noteDuration * 1.30;

if(outputTone)
{
    if(currentTime - previousToneTime >= noteDuration)
    {
      previousToneTime = currentTime;
      noTone(BUZZER_PIN);
      outputTone=false;
    }
}
else
{

  if(currentTime - previousToneTime >=pauseBetweenNotes)
  {
    previousToneTime=currentTime;
    tone(BUZZER_PIN,toneOut[thisNote]);
    outputTone = true;
    thisNote +=1;
      if(thisNote >=(sizeof(toneOut)/sizeof(toneOut[0])))
      {
        thisNote=0;
      }
  }
}
  

}



//========================================================================
//                         MOTOR CONTROL
//========================================================================



//STEPPER MOTORS
void stepperTurn(int mSelect,float steps)
{
/*  
 *     // step one revolution  in one direction:
  //Serial.println("clockwise");
  //myStepper.step(stepsPerRevolution);
  delay(500);

  // step one revolution in the other direction:
  Serial.println("counterclockwise");
  myStepper.step(-stepsPerRevolution);
  delay(500);
 */
shoulderLeft.run();
shoulderRight.run();
neckStepper.run();

//neckStepper.move(15);

if( shoulderLeft.stepsToGo() ==0 && shoulderRight.stepsToGo() == 0)
{
  switch(mSelect)
  {
    //BACKWARDS
    case 0:
      shoulderLeft.move( steps);
      shoulderRight.move(-steps);
    break;
    case 1://FORWARDS
        shoulderRight.move(steps);
        shoulderLeft.move(-steps);
    break;

    case 2:
    neckStepper.move(steps);
    break;
    case 3:
    neckStepper.move(-steps);
    default:
    break;
  }
}
 
  
}

// DC MOTORS
void wheelTurn(int pwr,int dir)
{
  
// Turn on motor A & B

if(pwr >255)
  pwr=255;
//Serial.println(pwr);  



switch(dir)
{
case 0: //FORWARD
  
  digitalWrite(in1, HIGH);
  digitalWrite(in2, LOW);
  digitalWrite(in3, LOW);
  digitalWrite(in4, HIGH);
  
  break;
// REVERSE
 case 1:


  digitalWrite(in1, LOW);
  digitalWrite(in2, HIGH);
  digitalWrite(in3, HIGH);
  digitalWrite(in4,LOW);

  break;
case 2:
  digitalWrite(in1, LOW);
  digitalWrite(in2, HIGH);
  digitalWrite(in3, LOW);
  digitalWrite(in4,HIGH);
  break;
 case 3:
  digitalWrite(in1, HIGH);
  digitalWrite(in2, LOW);
  digitalWrite(in3, HIGH);
  digitalWrite(in4,LOW);
  break; 

default:
  digitalWrite(in1, LOW);
  digitalWrite(in2, LOW);
  digitalWrite(in3, LOW);
  digitalWrite(in4, LOW);
  pwr=0;
  
//analogWrite(en1,pwr);
//analogWrite(en2,pwr);
break;

}   


analogWrite(en1,pwr);
analogWrite(en2,pwr);
//turn ON motor control TIMER
}

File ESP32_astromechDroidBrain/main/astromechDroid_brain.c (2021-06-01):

/* 
======================================================
		ASTROMECH DROID BRAIN
====================================================== 
   This started out as a Hello World Example
   but has morphed into something much different...

legal stuff i dont quite understand:

   This example code is in the Public Domain (or CC0 licensed, at your option.)

   Unless required by applicable law or agreed to in writing, this
   software is distributed on an "AS IS" BASIS, WITHOUT WARRANTIES OR
   CONDITIONS OF ANY KIND, either express or implied.
*/

#include <stdio.h>
#include <string.h>
#include "sdkconfig.h"
#include "freertos/FreeRTOS.h"
#include "freertos/task.h"
#include "esp_system.h"
#include "esp_spi_flash.h"


//ESP-Cam driver
#include "esp_camera.h"

//WiFi soft AP libraries
#include "esp_wifi.h"
#include "esp_event.h"
#include "esp_log.h"
#include "nvs_flash.h"

#include "lwip/err.h"
#include "lwip/sys.h"
#include "esp_netif.h"

//server libraries
//#include "protocol_examples_common.h"
#include <esp_http_server.h>

//SPIFFS and SD File support
#include <sys/unistd.h>
#include <sys/stat.h>
#include <sys/param.h>
#include "esp_spiffs.h"
#include "esp_netif.h"
#include "esp_err.h"
#include "esp_vfs_fat.h"
//#include "nvs_flash.h"
#include "sdkconfig.h"
//#include "driver/sdspi_host.h"
//#include "driver/spi_common.h"
//#include "sdmmc_cmd.h"
//#include "soc/soc_caps.h"
//#if SOC_SDMMC_HOST_SUPPORTED
//#include "driver/sdmmc_host.h"
//#endif

//I2C LCD Libraries
#include "driver/gpio.h"
#include "driver/i2c.h"
#include "esp32/rom/uart.h"
#include "smbus.h"
#include "i2c-lcd1602.h"
// # include " cJSON.h"

#ifdef USE_SPI_MODE
#define PIN_NUM_MISO 2
#define PIN_NUM_MOSI 15
#define PIN_NUM_CLK  14
#define PIN_NUM_CS   13
#endif

#define SPI_DMA_CHAN    1
#define SPI_DMA_CHAN    1

/* The examples use WiFi configuration that you can set via project configuration menu.

   If you'd rather not, just change the below entries to strings with
   the config you want - ie #define EXAMPLE_WIFI_SSID "mywifissid"
*/

// ESP32Cam (AiThinker) PIN Map
//#ifdef BOARD_ESP32CAM_AITHINKER

#define CAM_PIN_PWDN 32
#define CAM_PIN_RESET -1 //software reset will be performed
#define CAM_PIN_XCLK 0
#define CAM_PIN_SIOD 26
#define CAM_PIN_SIOC 27

#define CAM_PIN_D7 35
#define CAM_PIN_D6 34
#define CAM_PIN_D5 39
#define CAM_PIN_D4 36
#define CAM_PIN_D3 21
#define CAM_PIN_D2 19
#define CAM_PIN_D1 18
#define CAM_PIN_D0 5
#define CAM_PIN_VSYNC 25
#define CAM_PIN_HREF 23
#define CAM_PIN_PCLK 22

//#endif

// LCD1602
#define LCD_NUM_ROWS               2
#define LCD_NUM_COLUMNS            32
#define LCD_NUM_VISIBLE_COLUMNS    16

#define I2C_MASTER_NUM           I2C_NUM_0
#define I2C_MASTER_TX_BUF_LEN    0                     // disabled
#define I2C_MASTER_RX_BUF_LEN    0                     // disabled
#define I2C_MASTER_FREQ_HZ       100000
#define I2C_MASTER_SDA_IO        14  //CONFIG_I2C_MASTER_SDA
#define I2C_MASTER_SCL_IO        13  //CONFIG_I2C_MASTER_SCL
#define WRITE_BIT I2C_MASTER_WRITE              /*!< I2C master write */
#define ACK_CHECK_EN 0x1                        /*!< I2C master will check ack from slave*/

#define CONFIG_LCD1602_I2C_ADDRESS 0x27  //0x3F
#define ARDUINO_I2C_ADDRESS 0x5F //change to match Arduino Sketch

esp_netif_t *ap_netif = NULL;
//WiFi SSID
#define MY_ESP_WIFI_SSID      "roboFi"//CONFIG_ESP_WIFI_SSID
#define MY_ESP_WIFI_PASS     ""// CONFIG_ESP_WIFI_PASSWORD
#define MY_ESP_WIFI_CHANNEL  1 //CONFIG_ESP_WIFI_CHANNEL
#define MY_MAX_STA_CONN     3 // CONFIG_ESP_MAX_STA_CONN

static const char* TAG = "astromechDroid_BRAIN";

static camera_config_t camera_config = {
    .pin_pwdn = CAM_PIN_PWDN,
    .pin_reset = CAM_PIN_RESET,
    .pin_xclk = CAM_PIN_XCLK,
    .pin_sscb_sda = CAM_PIN_SIOD,
    .pin_sscb_scl = CAM_PIN_SIOC,

    .pin_d7 = CAM_PIN_D7,
    .pin_d6 = CAM_PIN_D6,
    .pin_d5 = CAM_PIN_D5,
    .pin_d4 = CAM_PIN_D4,
    .pin_d3 = CAM_PIN_D3,
    .pin_d2 = CAM_PIN_D2,
    .pin_d1 = CAM_PIN_D1,
    .pin_d0 = CAM_PIN_D0,
    .pin_vsync = CAM_PIN_VSYNC,
    .pin_href = CAM_PIN_HREF,
    .pin_pclk = CAM_PIN_PCLK,

    //XCLK 20MHz or 10MHz for OV2640 double FPS (Experimental)
    .xclk_freq_hz = 20000000,
    .ledc_timer = LEDC_TIMER_0,
    .ledc_channel = LEDC_CHANNEL_0,

    .pixel_format = PIXFORMAT_JPEG, //YUV422,GRAYSCALE,RGB565,JPEG
    .frame_size = FRAMESIZE_VGA,    //QQVGA-UXGA Do not use sizes above QVGA when not JPEG

    .jpeg_quality = 12, //0-63 lower number means higher quality
    .fb_count = 1       //if more than one, i2s runs in continuous mode. Use only with JPEG
};

static esp_err_t init_camera()
{
    //initialize the camera
    esp_err_t err = esp_camera_init(&camera_config);
    if (err != ESP_OK)
    {
        printf( "Camera Init Failed");
        return err;
    }

    return ESP_OK;
}

//=========================================================================
static void i2c_master_init(void)
{
    int i2c_master_port = I2C_MASTER_NUM;
    i2c_config_t conf={
    .mode = I2C_MODE_MASTER,
    .sda_io_num = I2C_MASTER_SDA_IO,
    .sda_pullup_en = GPIO_PULLUP_DISABLE,  // GY-2561 provides 10kΩ pullups
    .scl_io_num = I2C_MASTER_SCL_IO,
    .scl_pullup_en = GPIO_PULLUP_DISABLE,  // GY-2561 provides 10kΩ pullups
    .master.clk_speed = I2C_MASTER_FREQ_HZ
    };
    i2c_param_config(i2c_master_port, &conf);
    i2c_driver_install(i2c_master_port, conf.mode,
                       I2C_MASTER_RX_BUF_LEN,
                       I2C_MASTER_TX_BUF_LEN, 0);
}




void sendArduinoI2C_cmd( uint8_t *data_wr, size_t size)
{
//  i2c_master_init();
  i2c_port_t i2c_num = I2C_MASTER_NUM;
  uint8_t arduinoAddress = ARDUINO_I2C_ADDRESS;
	//I2C Write..

	ESP_LOGE(TAG,"Starting I2C to Arduino..");
	i2c_cmd_handle_t cmd = i2c_cmd_link_create();
	i2c_master_start(cmd);
	i2c_master_write_byte(cmd,(arduinoAddress<<1) | WRITE_BIT,ACK_CHECK_EN );
	i2c_master_write(cmd,data_wr,size,ACK_CHECK_EN);
	i2c_master_stop(cmd);

   esp_err_t ret = i2c_master_cmd_begin(i2c_num, cmd, 1000 / portTICK_RATE_MS);
	if(ret != ESP_OK)	
		ESP_LOGE(TAG,"SENDING TO ARDUINO FAILED X(");
 i2c_cmd_link_delete(cmd); 
//vTaskDelete(NULL);

}




void lcdPrintIP( void *pvParam)
{


i2c_master_init();
i2c_port_t i2c_num = I2C_MASTER_NUM;


uint8_t address = CONFIG_LCD1602_I2C_ADDRESS;

    // Set up the SMBus
    smbus_info_t * smbus_info = smbus_malloc();
    ESP_ERROR_CHECK(smbus_init(smbus_info, i2c_num, address));
    ESP_ERROR_CHECK(smbus_set_timeout(smbus_info, 1000 / portTICK_RATE_MS));

    // Set up the LCD1602 device with backlight off
    i2c_lcd1602_info_t * lcd_info = i2c_lcd1602_malloc();
    ESP_ERROR_CHECK(i2c_lcd1602_init(lcd_info, smbus_info, true,
                                     LCD_NUM_ROWS, LCD_NUM_COLUMNS, LCD_NUM_VISIBLE_COLUMNS));

    ESP_ERROR_CHECK(i2c_lcd1602_reset(lcd_info));


uint8_t custom1[8] = {
  0x00,
  0x00,
  0x00,
  0x00,
  0x1F,
  0x00,
  0x00,
  0x00
};
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
